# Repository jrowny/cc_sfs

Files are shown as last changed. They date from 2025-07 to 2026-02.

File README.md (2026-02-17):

# Advanced Filament Sensor for the Elegoo Carbon Centauri

The Carbon Centauri is a great budget printer, but its filament runout sensor is a simple binary switch which cannot detect filament movement. This means the printer will print in mid-air if the filament gets tangled, breaks after the sensor, or fails to feed for any reason. This project aims to mitigate that issue with only two parts and 4 wires.

## Alternative Solutions

There's an alternative and more advanced fork of this project called: [OpenFilamentSensor](https://github.com/harpua555/OpenFilamentSensor).

## Table of Contents

- [Advanced Filament Sensor for the Elegoo Carbon Centauri](#advanced-filament-sensor-for-the-elegoo-carbon-centauri)
  - [Table of Contents](#table-of-contents)
  - [How it works](#how-it-works)
  - [Video](#video)
  - [Parts List (affiliate links)](#parts-list-affiliate-links)
    - [Optional Parts](#optional-parts)
  - [Wiring (with stock runout detection)](#wiring-with-stock-runout-detection)
  - [Alternate Wiring](#alternate-wiring)
  - [Firmware Installation](#firmware-installation)
  - [WebUi](#webui)
  - [Setting the timeout (time without movement)](#setting-the-timeout-time-without-movement)
  - [3D printed case/adapter](#3d-printed-caseadapter)
  - [Known Issues / Todo](#known-issues--todo)
  - [Updating](#updating)
  - [Building from Source for unsupported boards](#building-from-source-for-unsupported-boards)
  - [Development](#development)
    - [Firmware](#firmware)
    - [Web UI](#web-ui)

## How it works

The Elegoo CC does not have an input for a filament movement sensor like the BTT SFS 2.0, but it does have an open websocket communication layer. Using a cheap off the shelf ESP32 with a Big Tree Tech SFS 2.0 as a replacment, we can track the status of the printer, detect that filament has stopped moving and send a Websocket command to pause the print. This is not as accurate as a direct firmware integration would be, and requires configuring a timeout relative to your print speed, but it can still save prints when configured correctly. The build is relatively simple, requiring only two GPIO pins, 5v, and ground connections.

## Video

Tutorial video for building this mod (https://www.youtube.com/watch?v=6JYKpZ3HX2Y)

## Parts List (affiliate links)

- [ESP32 S3 N8R2](https://amzn.to/4lHsUTo) for their performance, but really, any Esp32 module should work. Also tested with 4mb [ESP32 Wroom modules](https://amzn.to/4kjtDbU).
- [Big Tree Tech SFS 2.0](https://amzn.to/40uZ1wN)

### Optional Parts

- [JST-XH 3-pin connectors](https://amzn.to/4l4m1Ll) OR [PCB mount connectors](https://amzn.to/4ns8Ntx). These are only required if you wish to retain the stock runout functionality by wiring directly to the existing runout connector.
- [Electrocookie](https://amzn.to/4lqguyo) (or other) solderable PCB if you wish to do PCB mount connections rather than direct wiring

## Wiring (with stock runout detection)

_*WARNING:*_ Integrating with the stock wiring may void your Elegoo CC warranty. Do this at your own risk. Your printer may be different, make sure to validate with a multimeter before connecting any wires to the CC.

There are only 4 wires used in this project. All connectors are JST-XH 3 pin connectors, even though only 2 pins are used on each of the two SFS 2.0 connectors.

| Wire | Color |
| --- | ----- |
| Ground | Black |
| 5V power | Red |
| Runout | Blue  |
| Movement (motion) | Green |

The Elegoo runout sensor connector has 5v, ground, and runout input
Connect 5v from the elegoo to 5vin on esp32, and 5v on the SFS2.0
Connect ground from the elegoo to ground on SFS2.0 and the ESP32
Connect runout from the elegoo to pin 12 on the ESP32 and the blue wire on the SFS 2.0
Connect the green wire from the SFS 2.0 to pin 13 on the ESP32

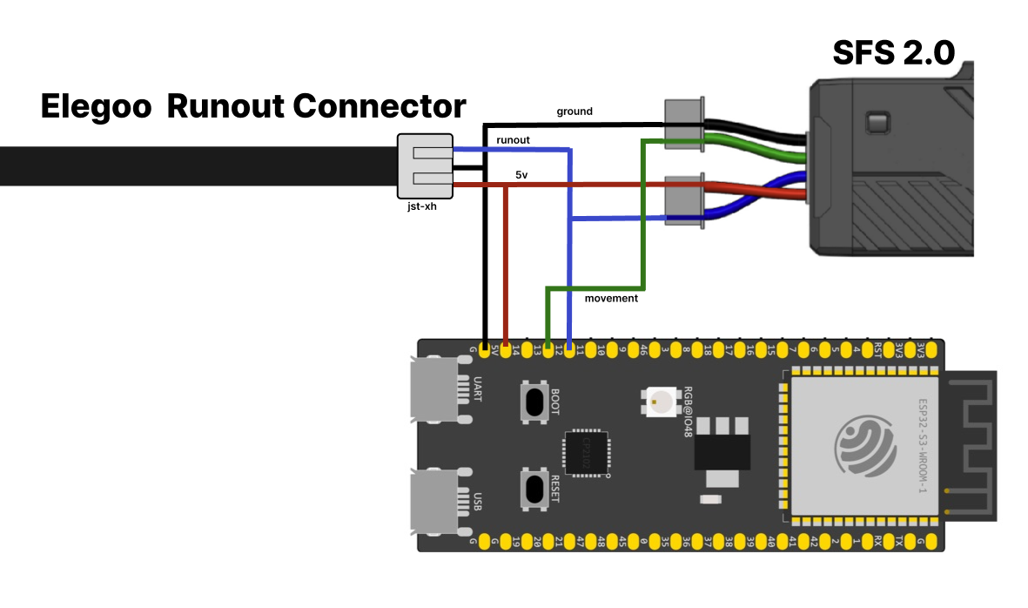
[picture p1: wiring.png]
Wiring Diagram


## Alternate Wiring

If you don't want to connect the device directly to the runout sensor, you may choose to simply disable the runout built-in runout detection and rely entirely on this project to pause the print. In that case, you can power the project from USB and connect the SFS wires to to the ESP32. Red to 5v, green to pin 13, blue to pin 12, and black to ground.

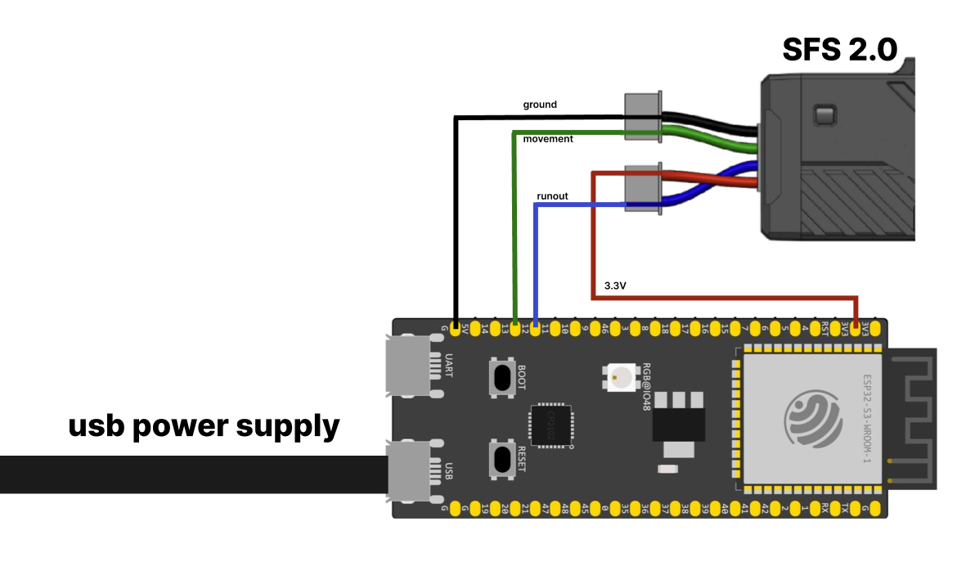
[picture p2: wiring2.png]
Wiring Diagram without connecting to Carbon


## Firmware Installation

1. Flash the firmware and filesystem, this can be done through the [web tool](https://jonathanrowny.com/cc_sfs/)
2. Once it's flashed, it will create a WiFi network called ElegooXBTTSFS20, connect to it with the password elegooccsfs20
3. Go to http://192.168.4.1 in your browser to load the user interface
4. Enter your wifi ssid, password, elegoo IP address and hit "save settings", the device will restart and connect to your network.
5. Access the web UI at anytime by going to http;//ccxsfs20.local

## WebUi

The WebUI shows the current status, whether filament has runout or stopped. It can be accessed by IP address or by going to [ccxsfs20.local](http://ccxsfs20.local) if you have mdns enabled on your network.

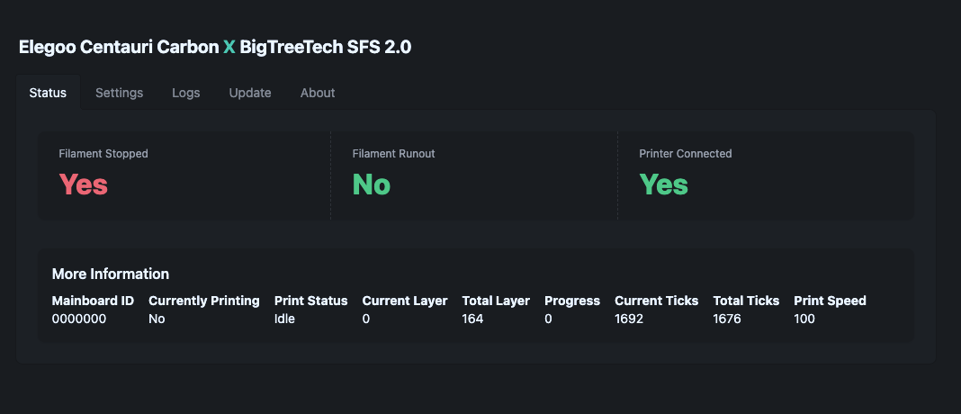
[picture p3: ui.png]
ui screenshot


## Setting the timeout (time without movement)

The BTT is meant to integrate with kipper or marlin firmware directly where the firmware knows how much filament _should_ be flowing. With the carbon, we can't know exactly how much it should be flowing, or at leaset, I haven't found a way. Therefore we use a timeout to aproximate how tolerant we should be to filament stopage. The BTT sensor reports an alternating value of HIGH/LOW (0/1) each time it detects the filament has moved 2.8mm. Each time it flips, we reset the timeout. If the value has not flipped after the timeout value has elapsed, the print is paused.

Setting the value too low, will mean that your prints might pause unexpectedly. Setting the value too high means your print may not be savable. Settings that impact the flow of your print may also require you to retune this value. The only way I've found to do this so far is to set the value low, start a test print, and then increase it until it reliably prints without pausing.

Note: the first layer uses 2 X Timeout because it is usually a slower flow layer and if you get a jam on your first layer, you're probably going to want to start over again anyway.

## 3D printed case/adapter

The files are available in [models](/models) directory or on [MakerWorld](https://makerworld.com/en/models/1594174-carbon-centauri-x-bigtreetech-sfs-2-0-mod)

## Known Issues / Todo

- [ ] Prints with ironing will fail, as there is no filament movement
- [ ] update from GH rather than using easyota
- [ ] use UDP ping to find/update Elegoo CC ip address like octoeverywhere does
- [ ] maybe integrate with octoeverywhere as an alternative client, so you don't need another rpi or docker container?
- [ ] support more boards like the Seeed Studio XIAO S3
- [ ] printhead cover fall protection

## Updating

Updates are available in the web ui in the update tab or by reflashing via the web tool, however, flashing through the webtool will erase all settings. Updating using the update section of the web ui will not override your settings as long as you use the `firmware-only.bin` from the [releases page](https://github.com/jrowny/cc_sfs/releases).

## Building from Source for unsupported boards

This project uses PlatformIO and building is as easy as adding the VSCode extension and hitting build. You can modify the `platformio.ini` file to support any custom board.

## Development

### Firmware

C++ code is a platformio project in `/src` folder. You can find more info [in their getting started guide](https://platformio.org/platformio-ide).

### Web UI

Web UI code is a [SolidJS](https://www.solidjs.com/) app with [vite](https://vite.dev/) in the `/webui` folder, it comes with a mock server. Just run `npm i && npm run dev` in the web folder.
Use `npm run build` in the `/web` folder to copy code into the `/data` folder, followed by `Upload file sytem image` command from PlatformIO

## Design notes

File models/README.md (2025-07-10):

# 3d printable adapter/case

This folder contains a little case to hold an ESP32 and the SFS 2.0 together. It has an optional snap-fit lid.

It requires a single m3 heat insert, if you want both screws. The Fusion360 file is also available.

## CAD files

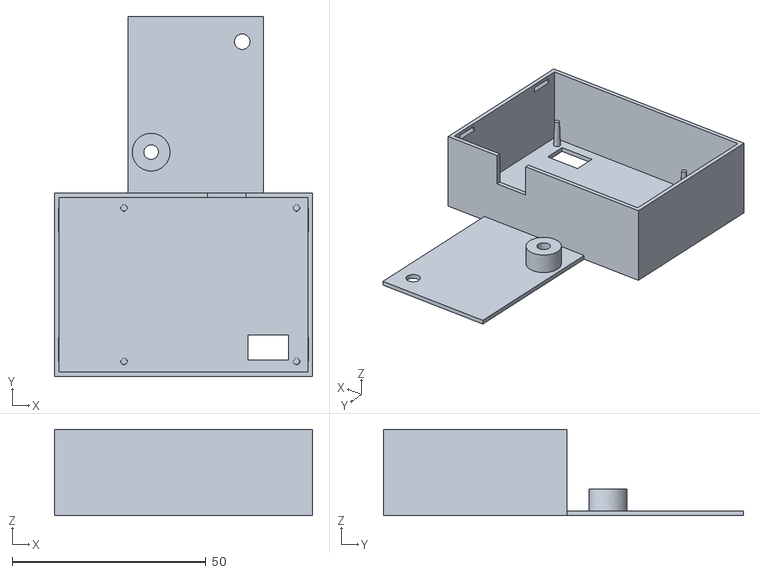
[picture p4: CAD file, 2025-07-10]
models/case.stl
66.7 x 92.9 x 22.2

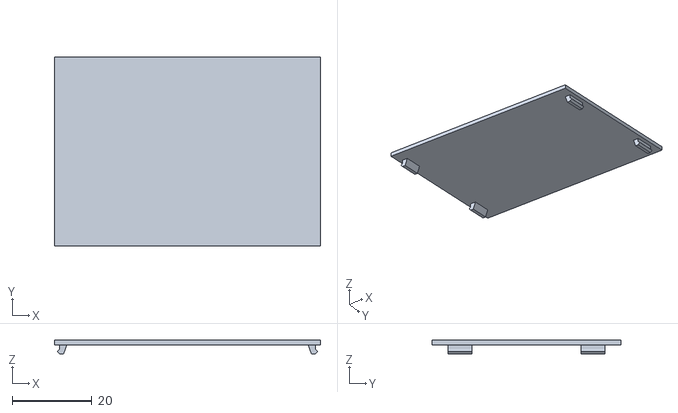
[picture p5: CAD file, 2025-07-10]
models/lid.stl
66.7 x 47.4 x 3.40

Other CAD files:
models/cc_sfs_adapter.f3d

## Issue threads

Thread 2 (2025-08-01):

Building for esp32-c3

dlarue, 2025-08-01:
I have a number of C3 boards and with the low pin count and performance needs I was wondering if you have insights on why this would not work on the ESP32-C3?

I'm OK with the simple answer. It's a great project and much needed as I've already had a filament knot issue.  I have the  connectors, BTT sensor and esp32-c3 plus crimping tool. WebUI wouldn't recognize the c3. But I have the Arduino v2 setup for esp32 and a CLI platform I configuration.

Thanks.

dlarue, 2025-08-02:
Looks like it'll build but is just a 70 bytes too big to fit in the program space of the esp32-c3.
 Builds to 1,310,798 bytes but only allowed 1,310,720 bytes). I added -0s before ${common.build-flags} but saw no difference in compiled size.

`Compiling .pio/build/lolin_c3_mini/FrameworkArduino/wiring_pulse.c.o
Compiling .pio/build/lolin_c3_mini/FrameworkArduino/wiring_shift.c.o
Archiving .pio/build/lolin_c3_mini/libFrameworkArduino.a
Indexing .pio/build/lolin_c3_mini/libFrameworkArduino.a
Linking .pio/build/lolin_c3_mini/firmware.elf
Retrieving maximum program size .pio/build/lolin_c3_mini/firmware.elf
Checking size .pio/build/lolin_c3_mini/firmware.elf
Advanced Memory Usage is available via "PlatformIO Home > Project Inspect"
Error: The program size (1310798 bytes) is greater than maximum allowed (1310720 bytes)
RAM:   [=         ]  12.5% (used 41084 bytes from 327680 bytes)
*** [checkprogsize] Explicit exit, status 1
Flash: [==========]  100.0% (used 1310798 bytes from 1310720 bytes)
`

dlarue, 2025-08-02:
Using the CLI for platformIO for both the esp32-c3 and the esp32-dev board I can compile and upload but the devices go into infinite reboots. Clearly something is different between the uploading the webUI does and what platformIO does.

~/.platformio/penv/bin/platformio run -e esp32-dev --target upload --upload-port /dev/ttyUSB0

booting looks like:
`rst:0x3 (SW_RESET),boot:0x13 (SPI_FAST_FLASH_BOOT)
configsip: 0, SPIWP:0xee
clk_drv:0x00,q_drv:0x00,d_drv:0x00,cs0_drv:0x00,hd_drv:0x00,wp_drv:0x00
mode:DIO, clock div:2
load:0x3fff0030,len:4604
ho 0 tail 12 room 4
load:0x40078000,len:15468
load:0x40080400,len:4
ho 8 tail 4 room 4
load:0x40080404,len:3180
entry 0x400805b8
E (556) esp_image: Image length 1312592 doesn't fit in partition length 1310720
E (556) boot: OTA app partition slot 0 is not bootable
E (556) esp_image: image at 0x150000 has invalid magic byte (nothing flashed here?)
E (564) boot: OTA app partition slot 1 is not bootable
E (568) boot: No bootable app partitions in the partition table
ets Jul 29 2019 12:21:46
`

The build env for esp32-dev is not unlike esp32-s3:
`[env:esp32-dev]
board = esp32dev
platform = ${common.platform}
framework = ${common.framework}
lib_compat_mode = strict
board_build.filesystem = littlefs
build_flags =
    ${common.build_flags}
lib_deps =
                ${common.lib_deps}

[env:esp32-build]
board = esp32dev
platform = ${common.platform}
framework = ${common.framework}
lib_compat_mode = strict
board_build.filesystem = littlefs
build_flags =
    ${common.build_flags}
lib_deps =
                ${common.lib_deps}
extra_scripts = merge_bin.py

`

dlarue, 2025-08-02:
Unfortunately trying to use the webUI locally failed also.

`~/cc_sfs/web$ npm i && npm run dev

up to date, audited 243 packages in 1s

32 packages are looking for funding
  run `npm fund` for details

found 0 vulnerabilities

> web@0.0.0 dev
> node devServer.js

✘ [ERROR] Unexpected end of file in JSON

    ../package.json:1:0:
      1 │
        ╵ ^

failed to load config from ~/cc_sfs/web/vite.config.ts
~/cc_sfs/web/node_modules/esbuild/lib/main.js:1477
  let error = new Error(text);
              ^

Error: Build failed with 1 error:
../package.json:1:0: ERROR: Unexpected end of file in JSON
    at failureErrorWithLog (~/cc_sfs/web/node_modules/esbuild/lib/main.js:1477:15)
    at ~/cc_sfs/web/node_modules/esbuild/lib/main.js:946:25
    at runOnEndCallbacks (~/cc_sfs/web/node_modules/esbuild/lib/main.js:1317:45)
    at buildResponseToResult (~/cc_sfs/web/node_modules/esbuild/lib/main.js:944:7)
    at ~/cc_sfs/web/node_modules/esbuild/lib/main.js:971:16
    at responseCallbacks.<computed> (~/cc_sfs/web/node_modules/esbuild/lib/main.js:623:9)
    at handleIncomingPacket (~/cc_sfs/web/node_modules/esbuild/lib/main.js:678:12)
    at Socket.readFromStdout `/cc_sfs/web/node_modules/esbuild/lib/main.js:601:7)
    at Socket.emit (node:events:517:28)
    at addChunk (node:internal/streams/readable:368:12) {
  errors: [Getter/Setter],
  warnings: [Getter/Setter]
}
`

dlarue, 2025-08-03:
I know this is now about building for esp32-dev option but it started as esp32-c3.
I got firmware.bin built with platformIO CLI to load using the webUI update( firmware only ) option.
I had to add the following built ops which I think shrunk it from 99% to 97% and that was enough for the webUI upload to show success.

`build_flags =
        ${common.build_flags}
        -D CORE_DEBUG_LEVEL=0
        ${env.build_flags}
        -D BOARD_FLASH_SIZE="4M"
        -D LTO
        -D Os
`

jrowny, 2025-08-05:
I don't have any C3 boards, but maybe I'll buy some and then I can add official support. If you'd like to submit a pull request I'll gladly accept it.

dlarue, 2025-08-06:
It builds but like with the WROOM32 I don't have the upload details figured out so the only way I could get running was with the WebUI which works with the WROOM32 and so does the WebUI upload/ElegantOTA if compiled to a small enough image.
Hmm, I don't think I tried either upload on the C3 with the debug level set to 0 so the image was smaller.
I've got like 5 C3 boards and only had 1 of the WROOM32 which I had planned to use in the car OBDII project. I'll order 3-5 more and keep them around because for these low pin count projects they are nice and small.

If I get one of the C3 boards working I'll submit a pull request.

jrowny, 2025-08-06:
you may need to adjust the partition sizes a bit. They're pre-set in platformio but you can override them.

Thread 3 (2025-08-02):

esp12E/esp8266

fredfred41, 2025-08-02:
Hi, same type of question as dlarue, do you think it could work, and be adapted to run on esp12e ? I have some, from a previous project, would be great if I could use one. thanks a lot

jrowny, 2025-08-05:
the esp8266 is a lot less powerful and this device must keep its websocket connection and web interface connection open reliably, so I'm not sure if it's a good idea to try on the esp8266.  You're free to give it a try, but I likely won't be able to support it.

Closed 2025-08-05.

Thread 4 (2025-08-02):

NTP is not synchronizing, can't connect to my wifi

fredfred41, 2025-08-02:
Hi, great job, I finally found a esp32. But I'm still interrested in using esp12e,  if it s possible and not too complicated to do.

So, I’m using an ESP32-WROOM-32D. I haven’t connected it to the printer or the SFS yet.
It’s flashed and powered by USB from my computer.
When I enter my Wi-Fi connection details, I get a red error message: "error saving settings, failed to fetch", and my ESP32 seems to restart, since the temporary Wi-Fi network disappears.

No new IP appears in my router’s list, and after a few minutes, the ElegooXBTTSFS20 Wi-Fi network reappears, so the connection to my Wi-Fi couldn’t be established.

However, in the settings, my Wi-Fi network name is saved, but the password field is still empty. I’m sure my credentials are correct, I pasted them from my password manager several times.

I don’t know if this is normal, but in the logs, the date for every entry is always 01/01/1970 01:00:00.

I tried to activate NTP Server on my routeur, same result.

Am I doing something wrong?

Thanks

01/01/1970 01:00:00: ESP SFS System starting up...
01/01/1970 01:00:00: Firmware version: 0.1.3
01/01/1970 01:00:00: Chip family: 1
01/01/1970 01:00:00: LittleFS filesystem initialized
01/01/1970 01:00:00: Starting AP mode
01/01/1970 01:00:00: NTP time synchronization started
01/01/1970 01:00:00: Web server started
01/01/1970 01:00:00: ElegooCC communication initialized
01/01/1970 01:00:00: System initialization complete
01/01/1970 01:00:00: Checking WiFi connection
01/01/1970 01:00:00: Skipping WiFi check in AP mode
01/01/1970 01:00:00: Filament movement stopped, last movement detected 4000ms ago
01/01/1970 01:00:00: Checking WiFi connection
01/01/1970 01:00:00: Skipping WiFi check in AP mode
01/01/1970 01:00:00: Checking WiFi connection
01/01/1970 01:00:00: Skipping WiFi check in AP mode
01/01/1970 01:00:00: Checking WiFi connection
01/01/1970 01:00:00: Skipping WiFi check in AP mode
01/01/1970 01:00:00: Checking WiFi connection

fredfred41, 2025-08-02:
Ok, so... My fault , my esp only support 2.4G I was trying to connect to 5G...
Thanks

Closed 2025-08-02.

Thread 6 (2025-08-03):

changing the CC IP address and saving does not result in connection to the CC

dlarue, 2025-08-03:
I had entered my CC IP address incorrectly and so was not seeing the connection in the log screen so I looked at the IP address, corrected the IP address error and saved the setting but the esp32 still did not connect to the CC.

After I hit the reset button on the ESP32 it then made connection with the CC and worked well after that.

Maybe there's an option in the code to trigger and update to the websocket creation so it gets the update without a reset.

jrowny, 2025-08-05:
thanks, I fixed this and should be in the next version.

Closed 2025-08-05.

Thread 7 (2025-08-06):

Filament Moving Stuck on Yes

beiyr, 2025-08-06:
I apologize for my slow response, everytime I thought about checking it I was already printing. Here are the logs. Note that all the starts are from me pushing the filament into the BTT. I am constantly moving it while it is inside.
`8/5/2025, 7:39:45 PM: Filament movement started
8/5/2025, 7:39:47 PM: Filament movement stopped, last movement detected 2000ms ago
8/5/2025, 7:39:49 PM: Filament movement started
8/5/2025, 7:39:51 PM: Filament movement stopped, last movement detected 2000ms ago
8/5/2025, 7:39:53 PM: Filament movement started
8/5/2025, 7:39:55 PM: Filament movement stopped, last movement detected 2000ms ago
8/5/2025, 7:39:57 PM: Filament movement started
8/5/2025, 7:39:59 PM: Filament movement stopped, last movement detected 2000ms ago
8/5/2025, 7:40:00 PM: Sending Ping
8/5/2025, 7:40:00 PM: Checking WiFi connection
8/5/2025, 7:40:02 PM: Filament movement started
8/5/2025, 7:40:05 PM: Filament movement stopped, last movement detected 2000ms ago
8/5/2025, 7:40:06 PM: Filament movement started
8/5/2025, 7:40:08 PM: Filament movement stopped, last movement detected 2000ms ago
8/5/2025, 7:40:09 PM: Filament movement started
8/5/2025, 7:40:11 PM: Filament movement stopped, last movement detected 2000ms ago
8/5/2025, 7:40:14 PM: Filament movement started
8/5/2025, 7:40:15 PM: Received status update:
8/5/2025, 7:40:20 PM: Filament movement stopped, last movement detected 2000ms ago
8/5/2025, 7:40:21 PM: Filament movement started
8/5/2025, 7:40:23 PM: Filament movement stopped, last movement detected 2000ms ago
8/5/2025, 7:40:24 PM: Filament movement started
8/5/2025, 7:40:26 PM: Filament movement stopped, last movement detected 2000ms ago
8/5/2025, 7:40:29 PM: Filament movement started
8/5/2025, 7:40:30 PM: Sending Ping
8/5/2025, 7:40:30 PM: Checking WiFi connection
8/5/2025, 7:40:34 PM: Filament movement stopped, last movement detected 2000ms ago
8/5/2025, 7:40:35 PM: Filament movement started
8/5/2025, 7:40:37 PM: Filament movement stopped, last movement detected 2000ms ago
8/5/2025, 7:40:40 PM: Filament movement started
8/5/2025, 7:40:42 PM: Filament movement stopped, last movement detected 2000ms ago
8/5/2025, 7:40:43 PM: Filament movement started
8/5/2025, 7:40:45 PM: Filament movement stopped, last movement detected 2000ms ago
8/5/2025, 7:40:45 PM: Filament movement started
8/5/2025, 7:40:47 PM: Filament movement stopped, last movement detected 2000ms ago
8/5/2025, 7:40:57 PM: Filament movement started
8/5/2025, 7:40:59 PM: Filament movement stopped, last movement detected 2000ms ago
8/5/2025, 7:41:00 PM: Sending Ping
8/5/2025, 7:41:00 PM: Checking WiFi connection
8/5/2025, 7:41:02 PM: Received status update:
8/5/2025, 7:41:03 PM: Filament movement started
8/5/2025, 7:41:05 PM: Filament movement stopped, last movement detected 2000ms ago
8/5/2025, 7:41:09 PM: Filament movement started
8/5/2025, 7:41:11 PM: Filament movement stopped, last movement detected 2000ms ago
8/5/2025, 7:41:15 PM: Filament movement started
8/5/2025, 7:41:17 PM: Filament movement stopped, last movement detected 2000ms ago
8/5/2025, 7:41:21 PM: Filament movement started
8/5/2025, 7:41:23 PM: Filament movement stopped, last movement detected 2000ms ago
8/5/2025, 7:41:30 PM: Sending Ping
8/5/2025, 7:41:30 PM: Checking WiFi connection
8/5/2025, 7:41:39 PM: Received status update:`

beiyr, 2025-08-06:
If so, is there a way to change it? I'm using jump cables and I can't really move those around.

beiyr, 2025-08-06:
I did the pinout for the first image which you deleted.

beiyr, 2025-08-06:
My wiring is to 13/14 instead of 13/12, as I went off of your first image.

jrowny, 2025-08-06:
that's the problem then, sorry about that! You can also just rebuild the image with a different pin configured by modifying platformio and building, there's no reason it can't work on 13/14.

I'm closing this issue, but feel free to reopen it if changing the pins doesn't work.

jrowny, 2025-08-06:
you'll need vscode and platformio extension. there's a tons of tutorials out there. Or you can just re-solder the wires onto the correct pins.

beiyr, 2025-08-07:
Do you think I can just keep 14 wired in, but add a jump cable to 12 for it? Or do I need to desolder 14? It's gonna be a pain to do I just want to see if I can do it the easy way.

Closed 2025-08-06.

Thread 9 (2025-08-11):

Bit of info about the Websocket

danielcherubini, 2025-08-11:
Hello from the Elegoo Home Assistant integration..

A little information for you, and sorry I didn't see any other way to let you know this. There's a kind of crappy limitation with the websocket, basically, 4 max connections, and video counts as a connection.

So, let's say you have your esp32 connected, AND you have your slicer, that's potentially 3 connections, now you visit the webui, and you're out of connections. (as it would be 5)

So how did we solve this? Well... we proxied it.

https://github.com/danielcherubini/elegoo-homeassistant/blob/main/custom_components/elegoo_printer/elegoo_sdcp/server.py

Proxied the discovery broadcast too..

If there's anything you want to know about the websocket connection, or the SCDP protocol just ask :D

jrowny, 2025-08-20:
thanks for the info!  I did know about this limitation but I should update the readme to call it out specifically. I need to install your HA integration, as I am a HA user.

I'm actually currently working on the serial interface on the motherboard to see if I can bypass the SDCP/web protocol altogether. There's 3 different MCUs on this thing and they all use different ways to talk to each other, so it's a bit tricky.

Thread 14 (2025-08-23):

Other issue with respect to filament run out option

pkdick, 2025-08-23:
Hello again,

As I wired your system using the Elegoo sensor's connector, I deactivated the option "Pause printing when filament runs out, rather than letting the Elegoo Centauri Carbon handle the runout". However when the filaments runs out, it is still pausing as it detects no more movement (as there are no more filament in the BIGTREETECH sensor): that is what I saw finishing a filament roll.

It seems that the printing speed is not properly detected as it is always set to 100 during a printing: if you could link the real printing speed with the sensor, that it could be possible to dynamically set the movement sensor timeout so this would reduce false alarms, couldn't you ?

Thank you for your support

Closed 2025-08-24.

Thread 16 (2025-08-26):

'Start Print Timeout' changes not updating over web interface

amenges, 2025-08-26:
I noticed that on the web interface I could update the 'Movement Sensor Timeout' but not the 'Start Print Timeout.'  When I click away and click back into settings or reload the 'Start Print Timeout' goes back to the default setting.  Does it have something to do with Settings.tsx where 'timeout' is used throughout so it can be updated but there are different variables for the other (startPrintTimeout, start_print_timeout)?

I am a big fan of this project!  I am new to this coding language / github, sorry if this has been addressed elsewhere or if I am missing something with how this program works.

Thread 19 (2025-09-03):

Wiring for esp32-wroom-32D

fredfred41, 2025-09-03:
Hi,

Thank you for this.

I have an esp32-wroom-32D, I managed to install it.

But can you please explain where I should connect the wire, it's not the same as your diagram.

Thanks a lot.

<a href="https://ibb.co/3mCFDN9T">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</a>

fredfred41, 2025-09-03:
ok forget it, using it with usb power :

<a href="https://ibb.co/VWJ64W04">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</a><br />

Thanks again for your work

Closed 2025-09-03.

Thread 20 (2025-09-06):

Wifi doesnt seem to come up?

burgleizer, 2025-09-06:
So I flashed the esp32 with the web tool(I think originally I tested with the pervious version) and when I go to console it seems everything is running but no wifi to connect to set up everything.  Any ideas? Is it a bad esp32?  I had it connected once for testing (with the old version)but since putting it on my Carbon(and flashing to the new version) I cant even see the wifi network for it.

Also after some more looking it looks like it might be broadcasting as a hidden network.  but i cant seem to connect to it with the ssid and password thats in the guide

burgleizer, 2025-09-06:
heres some logs.

[22:29:50]Firmware version: 0.1.7-beta
[22:29:50]Chip family: 1-S3
[22:29:50]LittleFS filesystem initialized
[22:29:50]Starting AP mode
[22:29:50]NTP time synchronization started
[22:29:50]Web server started
[22:29:53]ElegooCC communication initialized
[22:29:58]System initialization complete
[22:30:03]Checking WiFi connection
[22:30:08]Skipping WiFi check in AP mode
[22:30:13]Connecting to 192.168.1.123
[22:30:18]Filament has been detected
[22:30:28]Filament movement stopped, last movement detected 15023ms ago
[22:30:33]Disconnected from Carbon Centauri
[22:30:43]Checking WiFi connection
[22:30:48]Skipping WiFi check in AP mode
[22:30:53]Disconnected from Carbon Centauri
[22:31:03]Disconnected from Carbon Centauri
[22:31:06]ESP-ROM:esp32s3-20210327
[22:31:06]Build:Mar 27 2021
[22:31:06]rst:0x1 (POWERON),boot:0x8 (SPI_FAST_FLASH_BOOT)
[22:31:06]SPIWP:0xee
[22:31:06]mode:DIO, clock div:1
[22:31:06]load:0x3fce3808,len:0x4bc
[22:31:06]load:0x403c9700,len:0xbd8
[22:31:06]load:0x403cc700,len:0x2a0c
[22:31:06]entry 0x403c98d0
[22:31:06]ESP SFS System starting up...
[22:31:11]Firmware version: 0.1.7-beta
[22:31:16]Chip family: 1-S3
[22:31:21]LittleFS filesystem initialized
[22:31:26]Starting AP mode
[22:31:31]NTP time synchronization started
[22:31:36]Web server started
[22:31:41]ElegooCC communication initialized
[22:31:46]System initialization complete
[22:31:51]Checking WiFi connection
[22:31:56]Skipping WiFi check in AP mode
[22:32:01]Connecting to 192.168.1.123
[22:32:06]Filament has been detected
[22:32:16]Filament movement stopped, last movement detected 15023ms ago
[22:32:21]Disconnected from Carbon Centauri
[22:32:31]Checking WiFi connection
[22:32:36]Skipping WiFi check in AP mode
[22:32:41]Disconnected from Carbon Centauri
[22:32:51]Disconnected from Carbon Centauri
[22:33:01]Checking WiFi connection
[22:33:06]Skipping WiFi check in AP mode
[22:33:11]Disconnected from Carbon Centauri
[22:33:21]Disconnected from Carbon Centauri

Closed 2025-09-07.

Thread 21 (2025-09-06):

Issues I've run into

SShadow1974, 2025-09-06:
I have run into a few issues. #1 it seems the WebUI doesn't install the latest version of the firmware. I manually updated it which solves the original problems I had. Not going to go into those, since they're old news now. I had commented on your YouTube video, but perhaps that's not the best place to get your attention though you have replied to other comments. *shrug*
So, on to my current issues. My settings are 30000 wait on start up and my timeout is at 6000. I'm powering the ESP via USB and not using the OEM runout sensor.
#1 no matter what I set the startup timeout to, it will always pause somewhere between layer 1 and 2 on every print I've done.
#2 Sometimes when the printer is told to pause, "pausing..." will appear on the display and not go away. I have to power cycle the whole machine, after which it will recover and start printing again.
#3 It will randomly pause for no reason. The filament is running fine and isn't tangled. Unfortunately I don't have a cap of the error from the logs.

Suggestions
Longer log scroll back or a separate tab that retains errors so you can go back and look the error up.
List the version somewhere of the firmware somewhere so you can reference which version is installed on the ESP32

SShadow1974, 2025-09-06:
Well it just paused on me after I posted this. Here is a log:
`9/6/2025, 2:29:30 PM: Sending Ping
9/6/2025, 2:29:30 PM: Received status update:
9/6/2025, 2:29:33 PM: Received status update:
9/6/2025, 2:29:35 PM: Checking WiFi connection
9/6/2025, 2:29:36 PM: Filament movement stopped, last movement detected 6000ms ago
9/6/2025, 2:29:36 PM: Pause condition: 1
9/6/2025, 2:29:36 PM: Filament runout: 0
9/6/2025, 2:29:36 PM: Filament runout pause enabled: 1
9/6/2025, 2:29:36 PM: Filament stopped: 1
9/6/2025, 2:29:36 PM: Time since print start 1616789
9/6/2025, 2:29:36 PM: Is Machine status printing?: 1
9/6/2025, 2:29:36 PM: Print status: 13
9/6/2025, 2:29:36 PM: Pausing print, detected filament runout or stopped
9/6/2025, 2:29:36 PM: Waiting for acknowledgment for command 129 with request ID d94911415e2848ef96eae30c3482233f
9/6/2025, 2:29:36 PM: Command 129 acknowledged (Ack: 0) for request d94911415e2848ef96eae30c3482233f
9/6/2025, 2:29:36 PM: Received expected acknowledgment for command 129
9/6/2025, 2:29:36 PM: Pause condition: 1
9/6/2025, 2:29:36 PM: Filament runout: 0
9/6/2025, 2:29:36 PM: Filament runout pause enabled: 1
9/6/2025, 2:29:36 PM: Filament stopped: 1
9/6/2025, 2:29:36 PM: Time since print start 1617116
9/6/2025, 2:29:36 PM: Is Machine status printing?: 1
9/6/2025, 2:29:36 PM: Print status: 13
9/6/2025, 2:29:36 PM: Pausing print, detected filament runout or stopped
9/6/2025, 2:29:36 PM: Waiting for acknowledgment for command 129 with request ID 5d61ecdcf9b64c4c9f12cbecf18bf307
9/6/2025, 2:29:36 PM: Received status update:
9/6/2025, 2:29:36 PM: Command 129 acknowledged (Ack: 1) for request 5d61ecdcf9b64c4c9f12cbecf18bf307
9/6/2025, 2:29:36 PM: Received expected acknowledgment for command 129
9/6/2025, 2:29:36 PM: Pause condition: 1
9/6/2025, 2:29:36 PM: Filament runout: 0
9/6/2025, 2:29:36 PM: Filament runout pause enabled: 1
9/6/2025, 2:29:36 PM: Filament stopped: 1
9/6/2025, 2:29:36 PM: Time since print start 1617425
9/6/2025, 2:29:36 PM: Is Machine status printing?: 1
9/6/2025, 2:29:36 PM: Print status: 13
9/6/2025, 2:29:36 PM: Pausing print, detected filament runout or stopped
9/6/2025, 2:29:36 PM: Waiting for acknowledgment for command 129 with request ID 30d005d828514955b384dd928d78191d
9/6/2025, 2:29:36 PM: Received status update:
9/6/2025, 2:29:36 PM: Command 129 acknowledged (Ack: 1) for request 30d005d828514955b384dd928d78191d
9/6/2025, 2:29:36 PM: Received expected acknowledgment for command 129
9/6/2025, 2:29:37 PM: Filament movement started
9/6/2025, 2:29:40 PM: Received status update:
9/6/2025, 2:29:43 PM: Received status update:
9/6/2025, 2:29:43 PM: Filament movement stopped, last movement detected 6000ms ago
9/6/2025, 2:29:44 PM: Received status update:
9/6/2025, 2:30:00 PM: Sending Ping
9/6/2025, 2:30:05 PM: Checking WiFi connection
`

I checked the filament, there is no issue with the filament. Moving freely. This time it did not leave the "pausing..." on the screen, so I can resume it. Maybe a "RESUME PRINT" button could be added to the Web interface? Or is that just a one way communication from the ESP to the webbrowser?
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
SShadow1974, 2025-09-15:
And the current print finished without any further pauses. I'm going to take apart my sensor now and see if I see anything.

SShadow1974, 2025-09-16:
Ok, I took it apart. The only thing I saw is the light emitting diode was not straight off the board, it was bent a little upwards. So I bent it straight, tested it with a piece of filament and everything seems to be fine. The filament isn't slipping in the (for the lack of better words) gears and the web interface as well as the light on the SFS show when the filament is moving and when it's not. I even tried moving the filament VERY slowly - like I could feel the clicks when moving the filament and I would move it just one click and it would register the movement. So I'm now pretty sure it's not a hardware issue - unless bending that diode straight was the issue. I'll be doing a print later (waiting for some glue to dry) and will report back - again. :) Wish I could be more help.

SShadow1974, 2025-09-16:
And paused again, this time with a - ms reading. I think I may go back to the beta firmware. It worked better, I think.
9/16/2025, 12:23:51 AM: Filament movement stopped, last movement detected -335ms ago
9/16/2025, 12:23:51 AM: Pause condition: 1
9/16/2025, 12:23:51 AM: Filament runout: 0
9/16/2025, 12:23:51 AM: Filament runout pause enabled: 1
9/16/2025, 12:23:51 AM: Filament stopped: 1
9/16/2025, 12:23:51 AM: Time since print start 760134
9/16/2025, 12:23:51 AM: Is Machine status printing?: 1
9/16/2025, 12:23:51 AM: Print status: 13
9/16/2025, 12:23:51 AM: Pausing print, detected filament runout or stopped
9/16/2025, 12:23:51 AM: Waiting for acknowledgment for command 129 with request ID f952d314b557492a9c89639fbcbbdcea
9/16/2025, 12:23:51 AM: Filament movement started
9/16/2025, 12:23:51 AM: Command 129 acknowledged (Ack: 0) for request f952d314b557492a9c89639fbcbbdcea
9/16/2025, 12:23:51 AM: Received expected acknowledgment for command 129
9/16/2025, 12:23:52 AM: Received status update:
9/16/2025, 12:23:53 AM: Received status update:
9/16/2025, 12:23:56 AM: Received status update:
9/16/2025, 12:23:58 AM: Received status update:
9/16/2025, 12:24:05 AM: Sending Ping
9/16/2025, 12:24:09 AM: Filament movement stopped, last movement detected 15000ms ago

SShadow1974, 2025-09-16:
I don't know if any more of these log reports are of any use to you... But I'm back on the 0.2.2 firmware and it's still pausing. I've gone ahead and ordered another board from AliExpress. Until then, this is pretty much useless to me. :(
9/16/2025, 12:47:50 AM: Filament movement stopped, last movement detected -44ms ago
9/16/2025, 12:47:50 AM: Pause condition: 1
9/16/2025, 12:47:50 AM: Filament runout: 0
9/16/2025, 12:47:50 AM: Filament runout pause enabled: 1
9/16/2025, 12:47:50 AM: Filament stopped: 1
9/16/2025, 12:47:50 AM: Time since print start 353625
9/16/2025, 12:47:50 AM: Is Machine status printing?: 1
9/16/2025, 12:47:50 AM: Print status: 13
9/16/2025, 12:47:50 AM: Pausing print, detected filament runout or stopped
9/16/2025, 12:47:50 AM: Waiting for acknowledgment for command 129 with request ID 5b056ee9ba7f4274a9d397f2620a6be6
9/16/2025, 12:47:50 AM: Filament movement started
9/16/2025, 12:47:50 AM: Sending Ping
9/16/2025, 12:47:50 AM: Command 129 acknowledged (Ack: 0) for request 5b056ee9ba7f4274a9d397f2620a6be6
9/16/2025, 12:47:50 AM: Received expected acknowledgment for command 129
9/16/2025, 12:47:51 AM: Received status update:
9/16/2025, 12:47:52 AM: Received status update:
9/16/2025, 12:47:55 AM: Received status update:
9/16/2025, 12:47:58 AM: Received status update:
9/16/2025, 12:48:00 AM: Received status update:
9/16/2025, 12:48:07 AM: Filament movement stopped, last movement detected 15000ms ago

SShadow1974, 2025-09-25:
Well I just recieved a new SFS2.0. I'm just waiting on another ESP32 S3. I'm going to set up another sensor to rule out hardware issues. It simply does not work the way it is. I'm up to 30000 on both timeout settings and it will still randomly pause. On some prints, it'll print the whole thing. Other prints it stops after the first layer and then finishes. Other times it will pause over and over and over again. I just can't figure a common denominator with this. So I'm just going to rule out the issue being on my end.
Have you heard from anyone else that doesn't have ANY issues? Or is my experience common amoung all?

rhouri, 2025-09-28:
I have that issue as well. Restored the original filament sensor and issue disappeared.

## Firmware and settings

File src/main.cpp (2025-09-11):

#include <Arduino.h>
#include <ESPmDNS.h>
#include <WiFi.h>

#include "ElegooCC.h"
#include "LittleFS.h"
#include "Logger.h"
#include "SettingsManager.h"
#include "WebServer.h"
#include "improv.h"
#include "time.h"

#define SPIFFS LittleFS

#define STRINGIFY(x) #x
#define TOSTRING(x) STRINGIFY(x)

// Handle the case where environment variables are empty strings
#ifndef FIRMWARE_VERSION_RAW
#define FIRMWARE_VERSION_RAW dev
#endif
#ifndef CHIP_FAMILY_RAW
#define CHIP_FAMILY_RAW Unknown
#endif

// Create a macro that checks if the stringified value is empty and uses fallback
#define GET_VERSION_STRING(x, fallback) (strlen(TOSTRING(x)) == 0 ? fallback : TOSTRING(x))

const char* firmwareVersion = GET_VERSION_STRING(FIRMWARE_VERSION_RAW, "dev");
const char* chipFamily      = GET_VERSION_STRING(CHIP_FAMILY_RAW, "Unknown");

#define WIFI_CHECK_INTERVAL 30000     // Check WiFi every 30 seconds
#define WIFI_RECONNECT_TIMEOUT 10000  // Wait 10 seconds for reconnection
#define NTP_SYNC_INTERVAL 3600000     // Re-sync with NTP every hour (3600000 ms)

// NTP server to request epoch time
const char* ntpServer = "pool.ntp.org";

WebServer webServer(80);

// Variables to track WiFi connection monitoring
unsigned long lastWifiCheck      = 0;
unsigned long wifiReconnectStart = 0;
bool          isReconnecting     = false;

// These things get setup in the loop, not setup, so we need to track if they've happened
bool isWifiSetup      = false;
bool isElegooSetup    = false;
bool isWebServerSetup = false;
bool isNtpSetup       = false;

// Used by improv-wifi to parse serial data
uint8_t x_buffer[16];
uint8_t x_position = 0;

// Variables to track NTP synchronization
unsigned long lastNTPSyncAttempt = 0;

// If wifi fails, revert to AP mode and restart (only if never connected before);
void failWifi()
{
    // Only revert to AP mode if WiFi has never successfully connected
    if (!settingsManager.getHasConnected())
    {
        settingsManager.setAPMode(true);
        if (settingsManager.save())
        {
            logger.log("Failed to connect to wifi, reverted to AP mode (first connection attempt)");
        }
        else
        {
            logger.log("Failed to update settings");
        }

        delay(1000);  // Give time for serial output
        ESP.restart();
    }
    else
    {
        logger.log("WiFi connection failed, retrying in 30 seconds");
        // Don't restart, just continue trying to reconnect in checkWifiConnection()
    }
}

void startAPMode()
{
    logger.log("Starting AP mode");
    WiFi.softAP("ElegooXBTTSFS20", "elegooccsfs20");
    // Stop mDNS as it's not needed in AP mode
    MDNS.end();
}

void handleSuccessfulWifiConnection()
{
    logger.log("WiFi Connected");

    // Mark that WiFi has successfully connected at least once
    if (!settingsManager.getHasConnected())
    {
        settingsManager.setHasConnected(true);
        settingsManager.save();
        logger.log("First successful WiFi connection recorded");
    }

    // Reset any reconnection state
    isReconnecting = false;

    // Start/restart mDNS for station mode
    MDNS.end();
    if (!MDNS.begin("ccxsfs20"))
    {
        logger.log("Error setting up MDNS responder!");
    }
}

bool connectToWifiStation(bool isReconnect = false)
{
    const char* action = isReconnect ? "Reconnecting to" : "Connecting to";
    logger.logf("%s WiFi: %s", action, settingsManager.getSSID().c_str());

    WiFi.begin(settingsManager.getSSID().c_str(), settingsManager.getPassword().c_str());

    int attempts = 0;
    while (WiFi.status() != WL_CONNECTED && attempts < 30)
    {
        Serial.print('.');
        delay(1000);
        attempts++;
    }

    Serial.println();

    if (WiFi.status() == WL_CONNECTED)
    {
        handleSuccessfulWifiConnection();
        return true;
    }
    else
    {
        if (isReconnect)
        {
            logger.log("Failed to connect with new WiFi credentials");
        }
        else
        {
            failWifi();
        }
        return false;
    }
}

void cleanupWifiConnections()
{
    // Stop AP mode if it was running
    WiFi.softAPdisconnect(true);
    // Disconnect from any existing station connection
    WiFi.disconnect(true);
    delay(1000);
}

bool wifiSetup()
{
    if (settingsManager.isAPMode())
    {
        startAPMode();
        logger.log("Wifi setup in AP mode");
        return false;
    }
    else
    {
        return connectToWifiStation(false);
    }
}

bool reconnectWifiWithNewCredentials()
{
    logger.log("Applying new WiFi credentials...");

    // Clean up any existing connections first
    cleanupWifiConnections();

    // Check if we're switching to AP mode
    if (settingsManager.isAPMode())
    {
        logger.log("Switching to AP mode");
        startAPMode();
        return false;
    }

    // We're switching to or staying in station mode
    logger.log("Connecting to WiFi station mode with new credentials...");
    return connectToWifiStation(true);
}

void checkWifiConnection()
{
    logger.log("Checking WiFi connection");

    // Skip check if already in AP mode
    if (settingsManager.isAPMode())
    {
        logger.log("Skipping WiFi check in AP mode");
        return;
    }

    // Check if WiFi is connected
    if (WiFi.status() != WL_CONNECTED)
    {
        if (!isReconnecting)
        {
            logger.log("WiFi disconnected, attempting to reconnect...");
            WiFi.begin(settingsManager.getSSID().c_str(), settingsManager.getPassword().c_str());
            wifiReconnectStart = millis();
            isReconnecting     = true;
        }
        else
        {
            // Check if reconnection timeout has elapsed
            if (millis() - wifiReconnectStart >= WIFI_RECONNECT_TIMEOUT)
            {
                failWifi();
            }
        }
    }
    else
    {
        // WiFi is connected, reset reconnection state
        if (isReconnecting)
        {
            logger.log("WiFi reconnected successfully");
            isReconnecting = false;

            // Mark that WiFi has successfully connected at least once
            if (!settingsManager.getHasConnected())
            {
                settingsManager.setHasConnected(true);
                settingsManager.save();
            }
        }
    }
}

void setup()
{
    // put your setup code here, to run once:
    pinMode(FILAMENT_RUNOUT_PIN, INPUT_PULLUP);
    pinMode(MOVEMENT_SENSOR_PIN, INPUT_PULLUP);
    Serial.begin(115200);

    // Initialize logging system
    logger.log("ESP SFS System starting up...");
    logger.logf("Firmware version: %s", firmwareVersion);
    logger.logf("Chip family: %s", chipFamily);

    SPIFFS.begin();  // note: this must be done before wifi/server setup
    logger.log("Filesystem initialized");

    // Load settings early
    settingsManager.load();
    logger.log("Settings Manager Loaded");
}

void syncTimeWithNTP(unsigned long currentTime)
{
    struct tm timeinfo;
    lastNTPSyncAttempt = currentTime;
    if (getLocalTime(&timeinfo))
    {
        logger.log("NTP time synchronization successful");
    }
    else
    {
        logger.log("NTP time synchronization failed");
    }
}

unsigned long getTime()
{
    time_t now;
    time(&now);
    return now;
}

void onImprovErrorCallback(improv::Error err)
{
    logger.logf("Improv error: %d", err);
}

std::vector<std::string> getLocalUrl()
{
    return {// URL where user can finish onboarding or use device
            // Recommended to use website hosted by device
            String("http://" + WiFi.localIP().toString()).c_str()};
}

void getAvailableWifiNetworks()
{
    int networkNum = WiFi.scanNetworks();

    for (int id = 0; id < networkNum; ++id)
    {
        std::vector<uint8_t> data =
            improv::build_rpc_response(improv::GET_WIFI_NETWORKS,
                                       {WiFi.SSID(id), String(WiFi.RSSI(id)),
                                        (WiFi.encryptionType(id) == WIFI_AUTH_OPEN ? "NO" : "YES")},
                                       false);
        improv::send_response(data);
        delay(1);
    }
    // final response
    std::vector<uint8_t> data =
        improv::build_rpc_response(improv::GET_WIFI_NETWORKS, std::vector<std::string>{}, false);
    improv::send_response(data);
}

bool onImprovCommandCallback(improv::ImprovCommand cmd)
{
    switch (cmd.command)
    {
        case improv::Command::GET_CURRENT_STATE:
        {
            if ((WiFi.status() == WL_CONNECTED))
            {
                improv::set_state(improv::State::STATE_PROVISIONED);
                std::vector<uint8_t> data =
                    improv::build_rpc_response(improv::GET_CURRENT_STATE, getLocalUrl(), false);
                improv::send_response(data);
            }
            else
            {
                improv::set_state(improv::State::STATE_AUTHORIZED);
            }

            break;
        }

        case improv::Command::WIFI_SETTINGS:
        {
            if (cmd.ssid.length() == 0)
            {
                improv::set_error(improv::Error::ERROR_INVALID_RPC);
                break;
            }

            improv::set_state(improv::STATE_PROVISIONING);

            settingsManager.setSSID(cmd.ssid.c_str());
            settingsManager.setPassword(cmd.password.c_str());
            settingsManager.setAPMode(false);
            settingsManager.save(true);  // skip wifi check, we're about to try connecting

            if (reconnectWifiWithNewCredentials())  // connectWifi(cmd.ssid, cmd.password)
            {
                improv::set_state(improv::STATE_PROVISIONED);
                std::vector<uint8_t> data =
                    improv::build_rpc_response(improv::WIFI_SETTINGS, getLocalUrl(), false);
                improv::send_response(data);
            }
            else
            {
                improv::set_state(improv::STATE_STOPPED);
                improv::set_error(improv::Error::ERROR_UNABLE_TO_CONNECT);
            }

            break;
        }

        case improv::Command::GET_DEVICE_INFO:
        {
            std::vector<std::string> infos = {// Firmware name
                                              "CC_SFS",
                                              // Firmware version
                                              firmwareVersion,
                                              // Hardware chip/variant
                                              chipFamily,
                                              // Device name
                                              "CC_SFS"};
            std::vector<uint8_t>     data =
                improv::build_rpc_response(improv::GET_DEVICE_INFO, infos, false);
            improv::send_response(data);
            break;
        }

        case improv::Command::GET_WIFI_NETWORKS:
        {
            getAvailableWifiNetworks();
            break;
        }

        default:
        {
            improv::set_error(improv::ERROR_UNKNOWN_RPC);
            return false;
        }
    }

    return true;
}

bool handleImprovWifi()
{
    if (Serial.available() > 0)
    {
        uint8_t b = Serial.read();

        if (parse_improv_serial_byte(x_position, b, x_buffer, onImprovCommandCallback,
                                     onImprovErrorCallback))
        {
            x_buffer[x_position++] = b;
        }
        else
        {
            x_position = 0;
        }
        return true;
    }
    return false;
}

void loop()
{
    // handling immprovWifi should be the first thing we do
    if (handleImprovWifi())
    {
        // if we handled serial data, don't return so we don't bother with the rest of the setup
        return;
    }
    unsigned long currentTime     = millis();
    bool          isWifiConnected = !settingsManager.isAPMode() && WiFi.status() == WL_CONNECTED;

    if (!isWifiSetup)
    {
        isWifiSetup = wifiSetup();
        isWifiSetup = true;
        logger.log("Wifi setup complete");
        return;  //
    }
    if (!isWebServerSetup)
    {
        webServer.begin();
        isWebServerSetup = true;
        logger.log("Webserver setup complete");
        return;  //
    }

    // Check if WiFi reconnection is requested

    if (settingsManager.requestWifiReconnect)
    {
        settingsManager.requestWifiReconnect = false;
        reconnectWifiWithNewCredentials();
    }

    if (isWifiConnected)
    {
        if (!isElegooSetup)
        {
            elegooCC.setup();
            logger.log("Elegoo setup complete");
            isElegooSetup = true;
        }
        elegooCC.loop();

        if (!isNtpSetup)
        {
            configTime(0, 0, ntpServer);
            syncTimeWithNTP(currentTime);
            logger.log("NTP setup complete");
            isNtpSetup = true;
        }
        else if (currentTime - lastNTPSyncAttempt >= NTP_SYNC_INTERVAL)
        {
            syncTimeWithNTP(currentTime);
        }
    }
    else if (currentTime - lastWifiCheck >= WIFI_CHECK_INTERVAL)
    {
        checkWifiConnection();
    }

    webServer.loop();
}

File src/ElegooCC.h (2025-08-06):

#ifndef ELEGOOCC_H
#define ELEGOOCC_H

#include <Arduino.h>
#include <ArduinoJson.h>
#include <WebSocketsClient.h>

#include "UUID.h"

#define CARBON_CENTAURI_PORT 3030

// Pin definitions - can be overridden via build flags
#ifndef FILAMENT_RUNOUT_PIN
#define FILAMENT_RUNOUT_PIN 12
#endif

#ifndef MOVEMENT_SENSOR_PIN
#define MOVEMENT_SENSOR_PIN 13
#endif

// Status codes
typedef enum
{
    SDCP_PRINT_STATUS_IDLE          = 0,   // Idle
    SDCP_PRINT_STATUS_HOMING        = 1,   // Homing
    SDCP_PRINT_STATUS_DROPPING      = 2,   // Descending
    SDCP_PRINT_STATUS_EXPOSURING    = 3,   // Exposing
    SDCP_PRINT_STATUS_LIFTING       = 4,   // Lifting
    SDCP_PRINT_STATUS_PAUSING       = 5,   // Executing Pause Action
    SDCP_PRINT_STATUS_PAUSED        = 6,   // Suspended
    SDCP_PRINT_STATUS_STOPPING      = 7,   // Executing Stop Action
    SDCP_PRINT_STATUS_STOPED        = 8,   // Stopped
    SDCP_PRINT_STATUS_COMPLETE      = 9,   // Print Completed
    SDCP_PRINT_STATUS_FILE_CHECKING = 10,  // File Checking in Progress
    SDCP_PRINT_STATUS_PRINTING      = 13,  // Printing
    SDCP_PRINT_STATUS_UNKNOWN_15    = 15,  // unknown
    SDCP_PRINT_STATUS_HEATING       = 16,  // Heating
    SDCP_PRINT_STATUS_UNKNOWN_18    = 18,  // Unknown
    SDCP_PRINT_STATUS_UNKNOWN_19    = 19,  // Unknown
    SDCP_PRINT_STATUS_BED_LEVELING  = 20,  // Bed Leveling
    SDCP_PRINT_STATUS_UNKNOWN_21    = 21,  // Unknown
} sdcp_print_status_t;

// Extended Status Error Codes
typedef enum
{
    SDCP_PRINT_ERROR_NONE               = 0,  // Normal
    SDCP_PRINT_ERROR_CHECK              = 1,  // File MD5 Check Failed
    SDCP_PRINT_ERROR_FILEIO             = 2,  // File Read Failed
    SDCP_PRINT_ERROR_INVLAID_RESOLUTION = 3,  // Resolution Mismatch
    SDCP_PRINT_ERROR_UNKNOWN_FORMAT     = 4,  // Format Mismatch
    SDCP_PRINT_ERROR_UNKNOWN_MODEL      = 5   // Machine Model Mismatch
} sdcp_print_error_t;

typedef enum
{
    SDCP_MACHINE_STATUS_IDLE              = 0,  // Idle
    SDCP_MACHINE_STATUS_PRINTING          = 1,  // Executing print task
    SDCP_MACHINE_STATUS_FILE_TRANSFERRING = 2,  // File transfer in progress
    SDCP_MACHINE_STATUS_EXPOSURE_TESTING  = 3,  // Exposure test in progress
    SDCP_MACHINE_STATUS_DEVICES_TESTING   = 4,  // Device self-check in progress
} sdcp_machine_status_t;

typedef enum
{
    SDCP_COMMAND_STATUS                = 0,
    SDCP_COMMAND_ATTRIBUTES            = 1,
    SDCP_COMMAND_START_PRINT           = 128,
    SDCP_COMMAND_PAUSE_PRINT           = 129,
    SDCP_COMMAND_STOP_PRINT            = 130,
    SDCP_COMMAND_CONTINUE_PRINT        = 131,
    SDCP_COMMAND_STOP_FEEDING_MATERIAL = 132,
} sdcp_command_t;

// Struct to hold current printer information
typedef struct
{
    String              mainboardID;
    sdcp_print_status_t printStatus;
    bool                filamentStopped;
    bool                filamentRunout;
    int                 currentLayer;
    int                 totalLayer;
    int                 progress;
    int                 currentTicks;
    int                 totalTicks;
    int                 PrintSpeedPct;
    bool                isWebsocketConnected;
    bool                isPrinting;
    float               currentZ;
    bool                waitingForAck;
} printer_info_t;

class ElegooCC
{
   private:
    WebSocketsClient webSocket;
    UUID             uuid;

    String ipAddress;

    unsigned long lastPing;
    // Variables to track movement sensor state
    int           lastMovementValue;  // Initialize to invalid value
    unsigned long lastChangeTime;

    // machine/status info
    String              mainboardID;
    sdcp_print_status_t printStatus;
    uint8_t             machineStatusMask;  // Bitmask for active statuses
    int                 currentLayer;
    float               currentZ;
    int                 totalLayer;
    int                 progress;
    int                 currentTicks;
    int                 totalTicks;
    int                 PrintSpeedPct;
    bool                filamentStopped;
    bool                filamentRunout;

    unsigned long startedAt;

    // Acknowledgment tracking
    bool          waitingForAck;
    int           pendingAckCommand;
    String        pendingAckRequestId;
    unsigned long ackWaitStartTime;

    ElegooCC();

    // Delete copy constructor and assignment operator
    ElegooCC(const ElegooCC &)            = delete;
    ElegooCC &operator=(const ElegooCC &) = delete;

    void webSocketEvent(WStype_t type, uint8_t *payload, size_t length);
    void connect();
    void handleCommandResponse(JsonDocument &doc);
    void handleStatus(JsonDocument &doc);
    void sendCommand(int command, bool waitForAck = false);
    void pausePrint();
    void continuePrint();

    // Helper methods for machine status bitmask
    bool hasMachineStatus(sdcp_machine_status_t status);
    void setMachineStatuses(const int *statusArray, int arraySize);
    bool isPrinting();
    bool shouldPausePrint(unsigned long currentTime);
    void checkFilamentMovement(unsigned long currentTime);
    void checkFilamentRunout(unsigned long currentTime);

   public:
    // Singleton access method
    static ElegooCC &getInstance();

    void setup();
    void loop();

    // Get current printer information
    printer_info_t getCurrentInformation();
};

// Convenience macro for easier access
#define elegooCC ElegooCC::getInstance()

#endif  // ELEGOOCC_H

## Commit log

2025-07-08 add 10 second buffer after print status changes to started
2025-07-10 add 3d case model
    [case.stl, cc_sfs_adapter.f3d, lid.stl]
2025-07-14 clean up detection logic, skip pausing during last 50 ticks, clean up envs in build
    [ElegooCC.h]
2025-07-18 fix build for 8mb boards
2025-08-06 update wiring 2
2025-08-06 add xiao board
2025-08-25 Fix for enable/disable bug (full deactivation not possible #12)
    [WebServer.cpp]
2025-08-26 Fix for start print timeout not saving (https://github.com/jrowny/cc_sfs/issues/16)
    [WebServer.cpp]
2025-09-05 update build to use a matrix so we can add more board types easily
2025-09-05 don't revert to AP mode when wifi fails, if you've ever successfully connected
    [main.cpp]
2025-09-09 fix perf issue in timing
    [main.cpp]
2026-02-10 Add alternative solutions section to README
    Added a section for alternative solutions to the filament sensor issue.
